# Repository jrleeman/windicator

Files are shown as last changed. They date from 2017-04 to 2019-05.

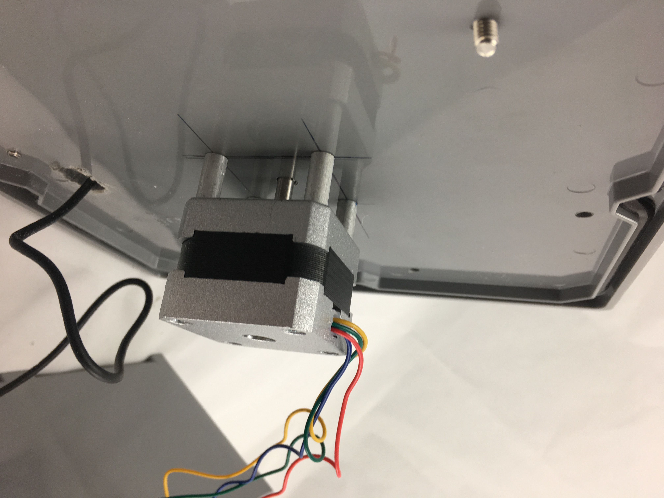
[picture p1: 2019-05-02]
build_photos/2017-04-22 12.01.30.jpg

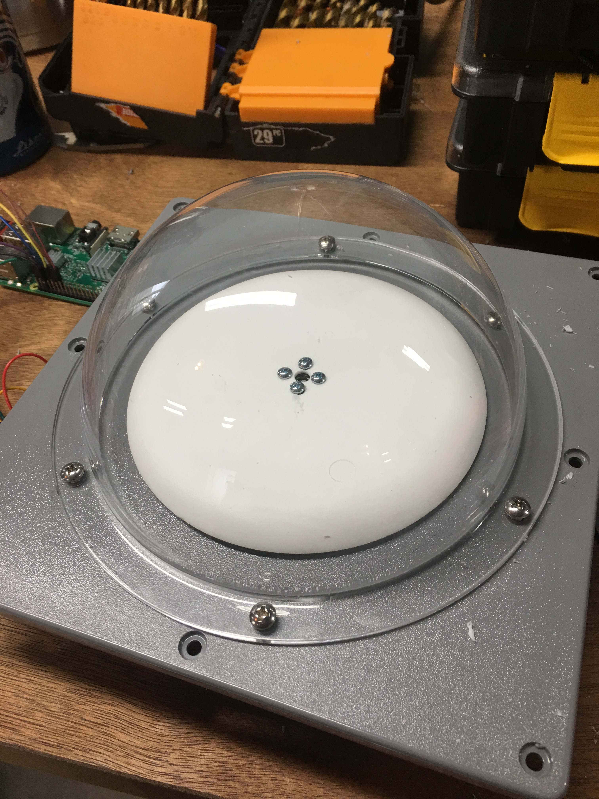
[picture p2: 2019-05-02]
build_photos/2017-04-22 11.04.38.jpg

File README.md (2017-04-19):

# Windicator

Windicator is the wind-pointing time lapse camera that is your window into the
atmosphere. Be sure to checkout all of the resources in this repository to
build your own.

* [Parts List](parts_list.md)
* [License](LICENSE)

## The Problem:
I want to create a tool to allow students or interested meteorology enthusiasts
to see the atmosphere flow and understand what is really happening then a front
or storm passes by. The atmosphere flows like a fluid with instabilities,
density currents, and many other phenomena that are fascinating but difficult to
follow due to their relatively slow movement. Static cameras are great, but
don't always follow the most interesting weather. 360 cameras are expensive,
produce a lot of data, and require the user to search for the most interesting
views.

## What the project does:
This project takes time-lapse photos of the atmosphere and combines them with
meteorological data on a webpage that can be easily explored. The camera is
continuously pointed in the direction the wind is blowing, so nature is steering
the lens to point at the most interesting phenomena in the area. The photos and
data can be explored at all levels from quick view to in-depth data analysis and
discussion.

## How it’s going to change the world:
Understanding the Earth is a monumental task and something that is not ingrained
in many people. With increasing urbanization and modernization, the intuition
and connection to natural processes gained through experience is all but gone.
This project helps speed up nature so we can experience how dynamic our
atmosphere is. In addition, it is designed to be inexpensive so that it is
accessible to schools, students, and hobbyists. By using 3D printing, open
source hardware and software, and modern design tools, the project can easily
tie into many portions of the STEM curriculum. Students can build a real and
useful scientific instrument and learn from the process and data. The time-lapse
videos can also be shared as a community resource.

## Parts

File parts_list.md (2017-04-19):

# Parts List

* 1x [Universal Mounting Hub - 5mm Aluminum](https://www.sparkfun.com/products/10006)
* 1x [Big Easy Stepper Driver](https://www.sparkfun.com/products/12859)
* 1x [NEMA 17 Stepper Motor](https://www.sparkfun.com/products/9238)
* 1x [US1881 Hall Effect Sensor](https://www.sparkfun.com/products/9312)
* 1x [Logitech C270 Webcam](http://amzn.to/2oVWhI1)
* 1x [Raspberry Pi 3 Model B](http://amzn.to/2onE3vI)
* 1x [Transcend 16GB MicroSDHC Class 10 UHS-1 Memory Card](http://amzn.to/2pCnNuT)
* 1x [6" Acrylic Hemisphere w/Holes](http://amzn.to/2o4fE2l)

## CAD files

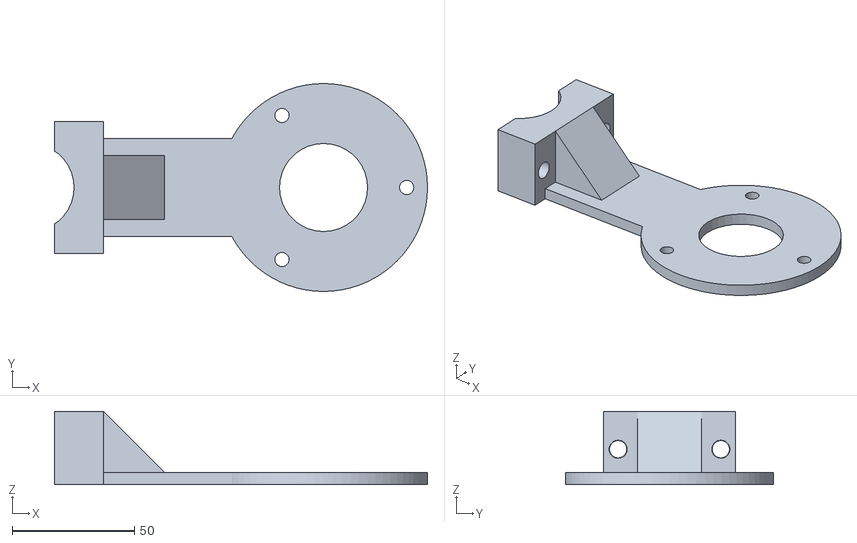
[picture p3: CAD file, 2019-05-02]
3d_printed_parts/Radiation_Shield_For_Weather_Station_Temperature_Humidity/Rad_Shd_Vert_mount_V1.stl
152.5 x 85.0 x 30.0

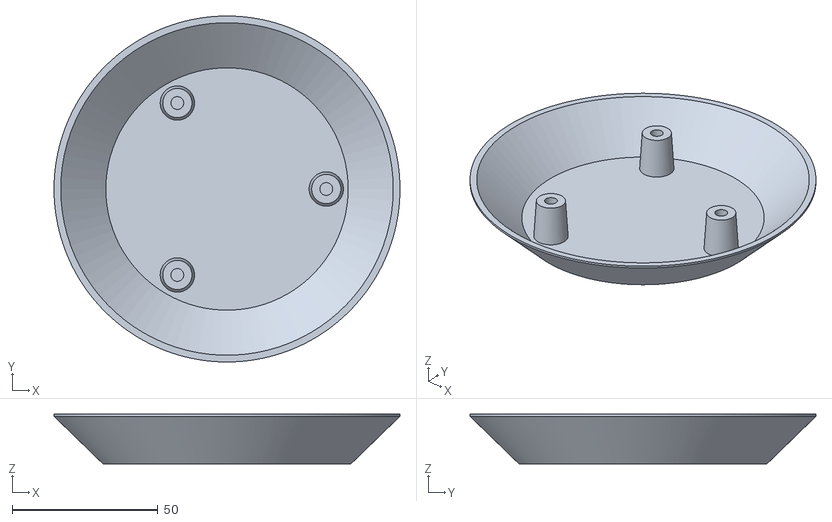
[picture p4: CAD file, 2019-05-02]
3d_printed_parts/Radiation_Shield_For_Weather_Station_Temperature_Humidity/Rad_Shd_Top_V1.stl
118.5 x 118.5 x 17.0

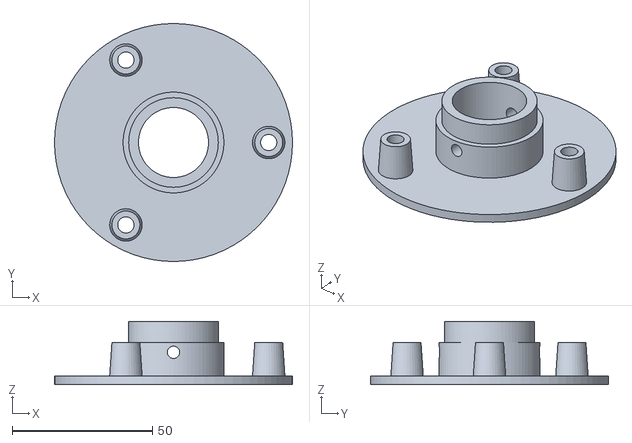
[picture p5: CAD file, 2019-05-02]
3d_printed_parts/Radiation_Shield_For_Weather_Station_Temperature_Humidity/Rad_Shd_Base_V1.stl
85.0 x 85.0 x 22.5

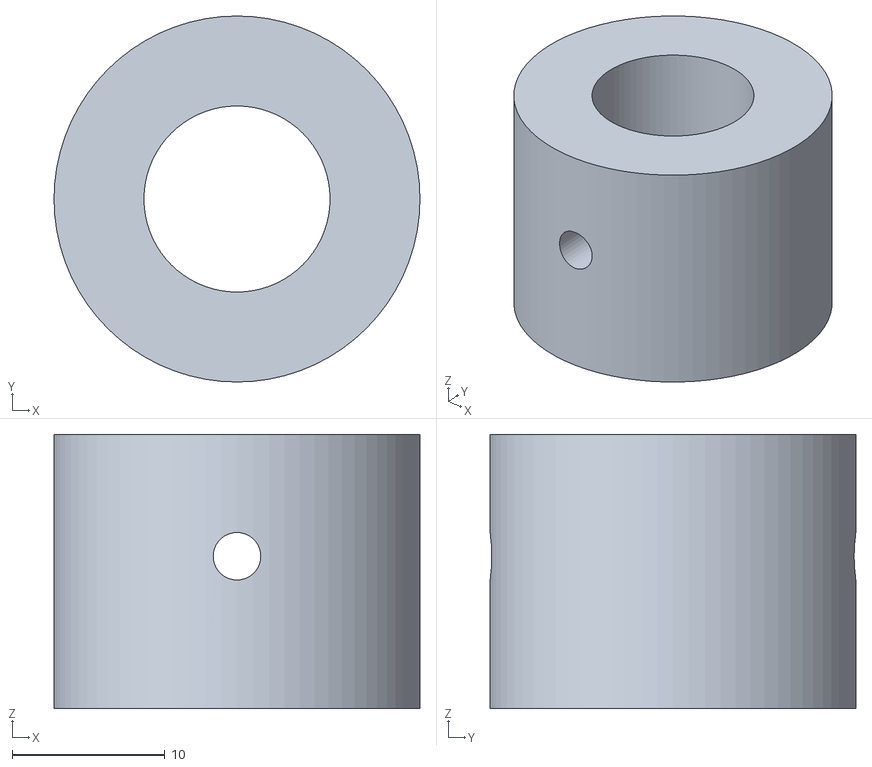
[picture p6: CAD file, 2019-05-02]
3d_printed_parts/Radiation_Shield_For_Weather_Station_Temperature_Humidity/HTM2500_mount_V1.stl
24.0 x 24.0 x 18.0

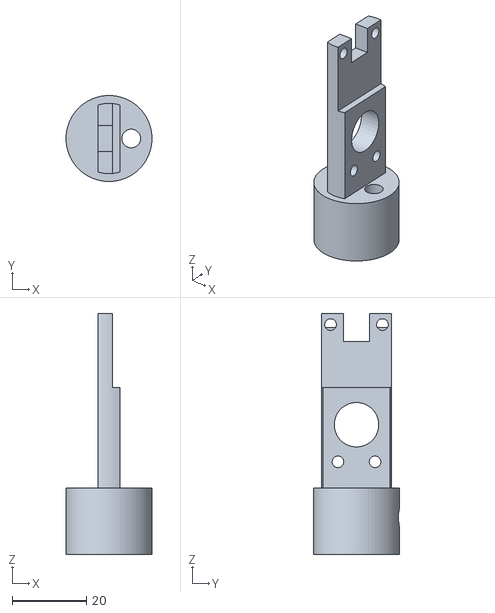
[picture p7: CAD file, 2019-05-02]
3d_printed_parts/Radiation_Shield_For_Weather_Station_Temperature_Humidity/SHT15_mount_V1.stl
23.2 x 23.2 x 65.0

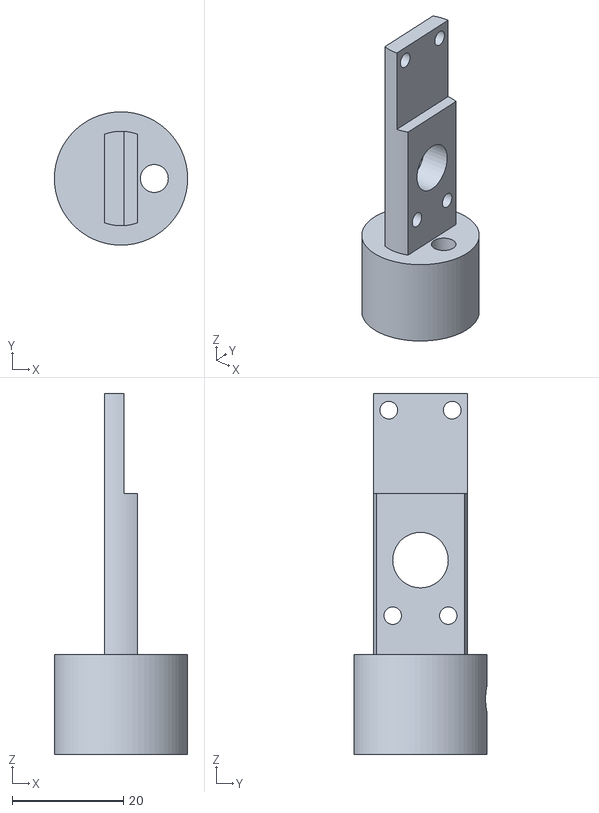
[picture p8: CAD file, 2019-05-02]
3d_printed_parts/Radiation_Shield_For_Weather_Station_Temperature_Humidity/HTU21D_mount_V1.stl
24.0 x 24.0 x 65.0

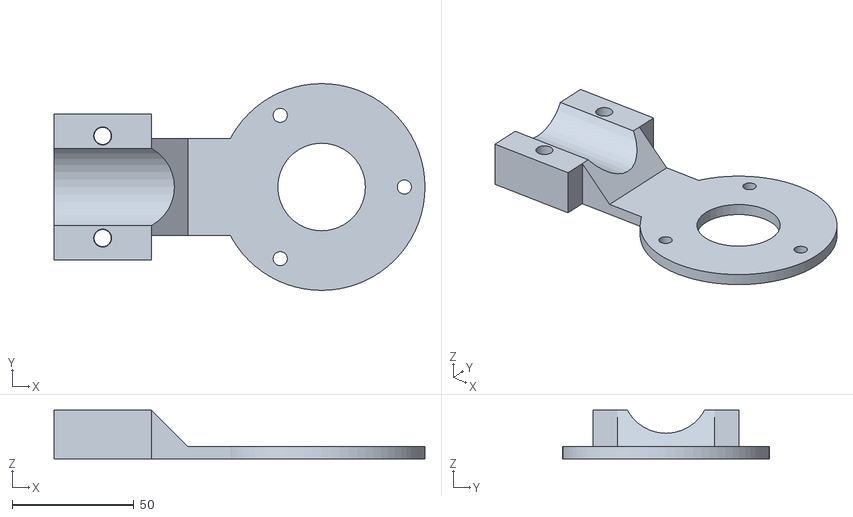
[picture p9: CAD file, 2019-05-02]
3d_printed_parts/Radiation_Shield_For_Weather_Station_Temperature_Humidity/Rad_Shd_Horz_mount_V1.stl
152.5 x 85.0 x 20.0

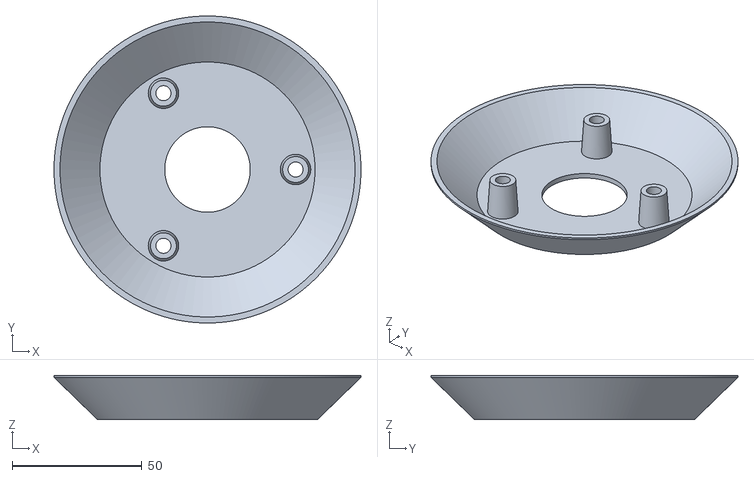
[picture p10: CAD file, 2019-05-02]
3d_printed_parts/Radiation_Shield_For_Weather_Station_Temperature_Humidity/Rad_Shd_Fin_V1.stl
118.5 x 118.5 x 17.0

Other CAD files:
3d_printed_parts/Radiation_Shield_For_Weather_Station_Temperature_Humidity/AM2315_mount_V1.stl

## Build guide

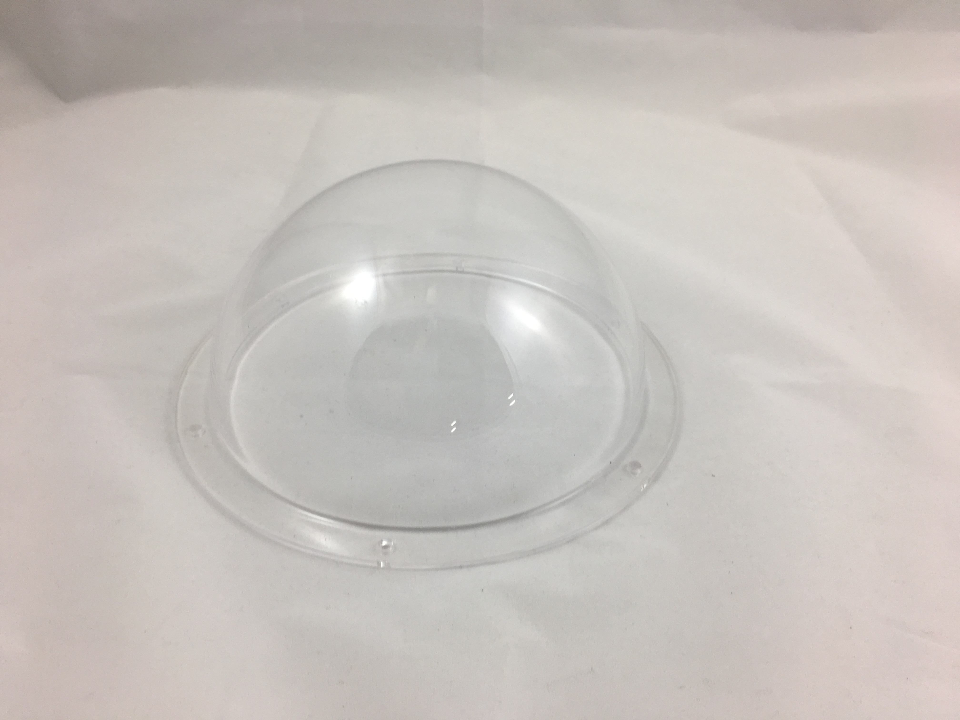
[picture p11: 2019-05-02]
build_photos/2017-04-22 08.41.16.jpg

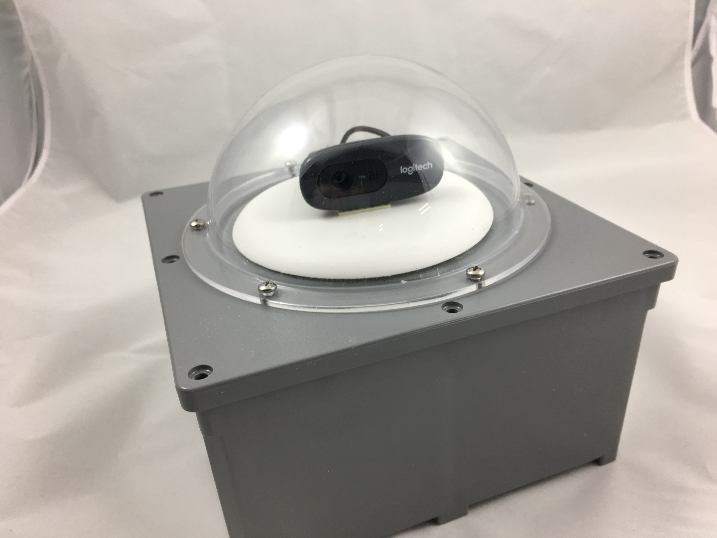
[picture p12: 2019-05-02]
build_photos/2017-04-22 12.01.10.jpg

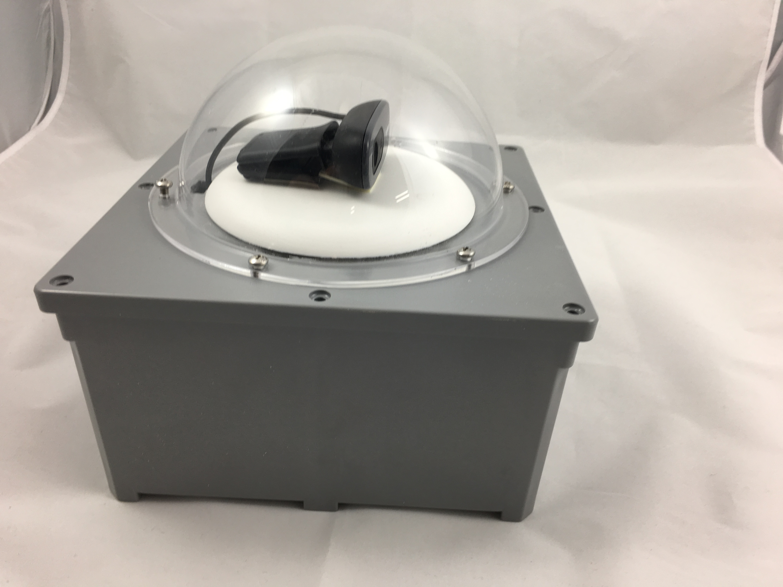
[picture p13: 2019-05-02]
build_photos/2017-04-22 12.01.16.jpg

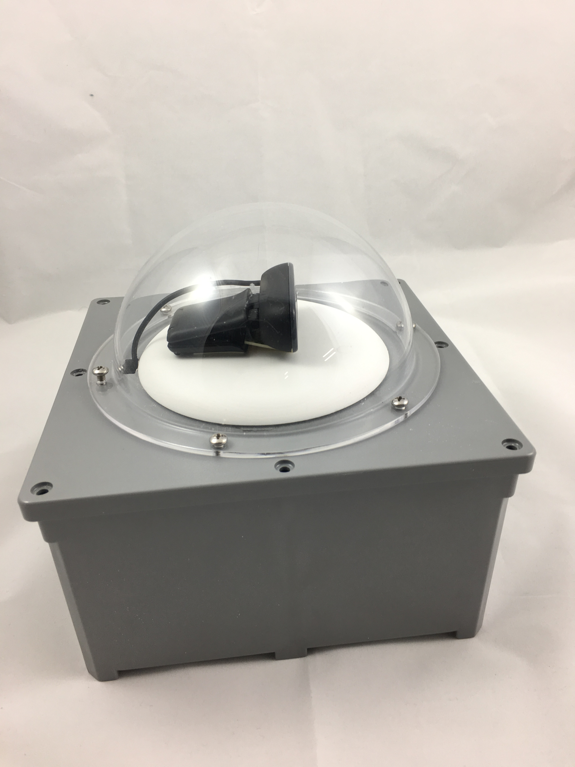
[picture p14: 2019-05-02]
build_photos/2017-04-22 12.01.18.jpg

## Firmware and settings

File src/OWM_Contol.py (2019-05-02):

import json
import os
from urllib2 import urlopen
from urllib import quote
#from urllib.request import urlopen
#from urllib.parse import quote
import time
import bigeasydriver
import RPi.GPIO as GPIO
import numpy as np
import datetime
import pygame
import pygame.camera
#import cv2


def get_weather(query):
    try:
        api_url = 'http://api.openweathermap.org/data/2.5/weather?q={0}&units=metric&appid={1}'
        query = quote(query)
        url = api_url.format(query, os.environ.get('OPENWXMAP_API_KEY', None))
        data = urlopen(url).read()#.decode('utf-8')
        parsed = json.loads(data)
        weather = None
        if parsed.get('weather'):
            weather = {'temperature':parsed['main']['temp'],
                       'humidity':parsed['main']['humidity'],
                       #'pressure':parsed['main']['sea_level'],
                       'windspeed':parsed['wind']['speed'],
                       'winddeg':parsed['wind']['deg']}
    except Exception as e:
        print("ERROR: ", e)
        weather = {'temperature':-999,
                   'humidity':-999,
                   #'pressure':parsed['main']['sea_level'],
                   'windspeed':-999,
                   'winddeg':0}
    return weather

def calculate_move(current_direction, new_direction):
    delta_degrees = new_direction - current_direction
    if current_direction + delta_degrees > 360:
        delta_degrees -= 360
        delta_degrees = delta_degrees * -1
    return delta_degrees, current_direction + delta_degrees


def move_camera(current_direction, move):
    """
    Positive = CCW
    """
    if move >0 :
        stepper.enable()
        stepper.set_direction('cw')
        actual_move = stepper.move_degrees(move)
        stepper.disable()

    elif move < 0:
        stepper.enable()
        stepper.set_direction('ccw')
        actual_move = stepper.move_degrees(np.abs(move))
        stepper.disable()

    else:
        stepper.disable()
        move = 0

    return current_direction + move


def take_photo(cam):
    cam.start()
    time.sleep(1)
    img = cam.get_image()
    utc_time = datetime.datetime.utcnow()
    img_fname = datetime.datetime.strftime(utc_time, 'images/%Y-%m-%dT%H:%M.jpg')
    pygame.image.save(img, img_fname)
    cam.stop()

if __name__ == '__main__':

    # Setup the big easy driver
    stepper = bigeasydriver.BigEasyDriver()
    stepper.enable_pin = 5
    stepper.MS1_pin = 6
    stepper.MS2_pin = 13
    stepper.MS3_pin = 19
    stepper.direction_pin = 26
    stepper.step_pin = 16

    stepper.begin()
    stepper.degrees_per_step = 1.8
    stepper.set_stepsize('full step')
    stepper.disable()

    # Setup camera
    pygame.camera.init()
    print("Cameras: ", pygame.camera.list_cameras())
    cam = pygame.camera.Camera("/dev/video0",(1024, 576))
    

    # Start with everything pointing at 180`
    current_direction = 180.
    while True:
        # Get weather
        weather = get_weather('Mead,CO')

        # Calculate move
        delta_degrees, current_direction = calculate_move(current_direction, weather['winddeg'])
        print("Moving {0} to point to {1} ".format(delta_degrees, current_direction))

        # Point into wind
        move_camera(current_direction, delta_degrees)

        # Take photo
        take_photo(cam)

        # Wait for next minute
        time.sleep(60)

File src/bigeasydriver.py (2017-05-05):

# Copyright (c) 2017-2025 John R. Leeman
# Distributed under the terms of the MIT License.

"""Control the Big Easy Driver (BED)

Contains tools to control stepper motors with the Big Easy Driver by Brian
Schmalz. For more information on the BED visit www.schmalzhaus.com/BigEasyDriver
"""
from math import floor

import RPi.GPIO as GPIO
from time import sleep

class BigEasyDriver(object):
    r"""The Big Easy Driver.

    This class contains information on connections and control methods for the
    BED.
    """

    def __init__(self):
        # Hardware pin connections
        self.enable_pin = None
        self.MS1_pin = None
        self.MS2_pin = None
        self.MS3_pin = None
        self.reset_pin = None
        self.sleep_pin = None
        self.step_pin = None
        self.direction_pin = None

        # Hardware state information
        self.isenabled = True
        self.direction = 'ccw'
        self.step_size = 'sixteenth step'
        self.isasleep = False
        self.isinreset = False
        self.microsteps_per_step = 16

        # Motor information
        self.degrees_per_step = None


    def begin(self):
        """
        Actually initialze the hardware pin states once they are set.
        """
        GPIO.setmode(GPIO.BCM) # Broadcom pin-numbering scheme
        if self.enable_pin is not None:
            GPIO.setup(self.enable_pin, GPIO.OUT)
            GPIO.output(self.enable_pin, GPIO.LOW)
        if self.MS1_pin is not None:
            GPIO.setup(self.MS1_pin, GPIO.OUT)
            GPIO.output(self.MS1_pin, GPIO.HIGH)
        if self.MS2_pin is not None:
            GPIO.setup(self.MS2_pin, GPIO.OUT)
            GPIO.output(self.MS2_pin, GPIO.HIGH)
        if self.MS3_pin is not None:
            GPIO.setup(self.MS3_pin, GPIO.OUT)
            GPIO.output(self.MS3_pin, GPIO.HIGH)
        if self.reset_pin is not None:
            GPIO.setup(self.reset_pin, GPIO.OUT)
            GPIO.output(self.reset_pin, GPIO.HIGH)
        if self.sleep_pin is not None:
            GPIO.setup(self.sleep_pin, GPIO.OUT)
            GPIO.output(self.sleep_pin, GPIO.HIGH)
        if self.step_pin is not None:
            GPIO.setup(self.step_pin, GPIO.OUT)
            GPIO.output(self.step_pin, GPIO.HIGH)
        if self.direction_pin is not None:
            GPIO.setup(self.direction_pin, GPIO.OUT)
            GPIO.output(self.direction_pin, GPIO.HIGH)


    def enable(self):
        """
        Enable the BED driver chip and final drive circuits.
        """
        # Enabled when enable is low. There is a 20k pulldown on the BED, so we
        # can let it float or pull it low. I chose to pull it low.
        GPIO.output(self.enable_pin, GPIO.LOW)
        self.isenabled = True
        return True

    def disable(self):
        """
        Disable the BED final drive ciruits.
        """
        GPIO.output(self.enable_pin, GPIO.HIGH)
        self.isenabled = False
        return True


    def set_stepsize(self, step_size):
        """
        Set the step size the motor will take.

        Options: full step, half step, quarter step, eigth step, sixteenth step
        """
        self.step_size = step_size
        microstep_pins = [self.MS1_pin, self.MS2_pin, self.MS3_pin]

        microstep_pin_states = {'full step': [GPIO.LOW, GPIO.LOW, GPIO.LOW],
                                'half step': [GPIO.HIGH, GPIO.LOW, GPIO.LOW],
                                'quarter step': [GPIO.LOW, GPIO.HIGH, GPIO.LOW],
                                'eigth step': [GPIO.HIGH, GPIO.HIGH, GPIO.LOW],
                                'sixteenth step': [GPIO.HIGH, GPIO.HIGH, GPIO.HIGH]}

        microsteps_per_step = {'full step': 1, 'half step': 2, 'quarter step':4,
                               'eigth step': 8, 'sixteenth step':16}

        try:
            microstep_states = microstep_pin_states[self.step_size]
            self.step_size = step_size
            self.microsteps_per_step = microsteps_per_step[self.step_size]
        except KeyError:
            raise ValueError('Unkown option for step_size: {0}'.format(self.step_size))

        # Actually toggle the outputs
        for pin, state in zip(microstep_pins, microstep_states):
            GPIO.output(microstep_pins, microstep_states)

        return True


    def set_direction(self, direction):
        """
        Set the direction of motor rotation.

        Input is tied high on the BED
        """
        direction_pin_states = {'ccw': GPIO.HIGH,
                                'cw': GPIO.LOW}
        try:
            direction_state = direction_pin_states[direction]
            self.direction = direction
        except KeyError:
            raise ValueError('Unknown direction: {0}'.format(direction))

        # Actually set the pin state
        GPIO.output(self.direction_pin, direction_state)
        return True


    def step(self):
        """
        Move the motor by one step.

        Motor steps on the rising edge on the rising edge. The pulse must be at
        least 1us high and 1us low.
        """
        GPIO.output(self.step_pin, GPIO.LOW)
        sleep(3e-3)
        GPIO.output(self.step_pin, GPIO.HIGH)
        sleep(3e-3)
        return True


    def move_nsteps(self, nsteps):
        """
        Move the motor by nsteps.

        Motor steps on the rising edge on the rising edge. The pulse must be at
        least 1us high and 1us low.
        """
        for i in range(nsteps):
            self.step()
        return True

    def move_degrees(self, degrees, dynamic_stepsize=False):
        """
        Move the motor a specified number of degrees.

        Returns the acutal amount moved.
        """
        if dynamic_stepsize:
            total_degrees_moved = 0.
            initial_stepsize = self.step_size
            # Start with full steps
            self.set_stepsize('full step')
            nsteps = int(floor((degrees - total_degrees_moved)/ (self.degrees_per_step / self.microsteps_per_step)))
            print("steos: ", nsteps, self.microsteps_per_step)
            self.move_nsteps(nsteps)
            total_degrees_moved += nsteps * (self.degrees_per_step / self.microsteps_per_step)
            print("moved: ", total_degrees_moved)
            
            # Half steps
            self.set_stepsize('half step')
            nsteps = int(floor((degrees - total_degrees_moved)/ (self.degrees_per_step / self.microsteps_per_step)))
            self.move_nsteps(nsteps)
            print("steos: ", nsteps, self.microsteps_per_step)
            total_degrees_moved += nsteps * (self.degrees_per_step / self.microsteps_per_step)
            print("moved: ", total_degrees_moved)
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

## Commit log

2017-05-05 Initial cut at BED drivers
2017-05-05 Add simple test for big easy driver
2017-05-05 Sketch of cv2 camera capture
2017-05-05 Use PyGame for camera capture
2019-05-02 Add build photos
    [AM2315_mount_V1.stl, HTM2500_mount_V1.stl, HTU21D_mount_V1.stl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]
